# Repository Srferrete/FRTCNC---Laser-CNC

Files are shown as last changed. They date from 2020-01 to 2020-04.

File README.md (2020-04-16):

# Laser-CNC
Maquina Cnc para poder poner un laser y hacer grabados 

Estamos creando un Laser cnc, que pueda ser construido a mediante piezas impresas en 3d y material basico con el fin de que sea lo más sencilla de montar y lo más barata posible.

Es un proyecto que ya hicimos el pasado, pero esta vez le hemos dado una vuelta para que quede lo más vistoso posible además de hacer una estructura un poco más fuerte.

La base de la maquina es basante sencilla, vas a usar Perfiles V-slot, perfilería de aluminio y materiales basicos.
En cuanto a electronica usaremos un Mks DLC con driver Drv8825 y como FirmWare nos basaremos en GRBL.
MONTAJE
Todo el montaje y configuración lo podeis encontrar en mi canal de youtube, no os lo perdais y suscribiros.
https://www.youtube.com/playlist?list=PL0HtuDn0Yw6M-yycOaHozkW66rjWwoKbI

FIRMWARE
Para instalar el firmware en la MKS DLC, necesitais instalar el IDE de arduino que podeis encontrar aqui https://www.arduino.cc/
Una vez instalado, copiar la carpeta grbl en en C:\Users\VUESTRO_USUARIO\Documents\Arduino\libraries. De esta manera os funcionará como lo hacemos en el video.

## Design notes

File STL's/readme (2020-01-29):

Esta Carpeta Os dejo todos los stl relacionanos con la máquina laser aunque tambien los podeis encontrar en thingiverse(está pendiente de subir)
Tambien os iré dejando por aquí enlaces a piezas de thingiverse que usado para mi cnc, como por ejemplo
el soporete de los finales de carrera

PIEZAS DE OTROS DISEÑADORES

soporte finales de carrera -- https://www.thingiverse.com/thing:3147644

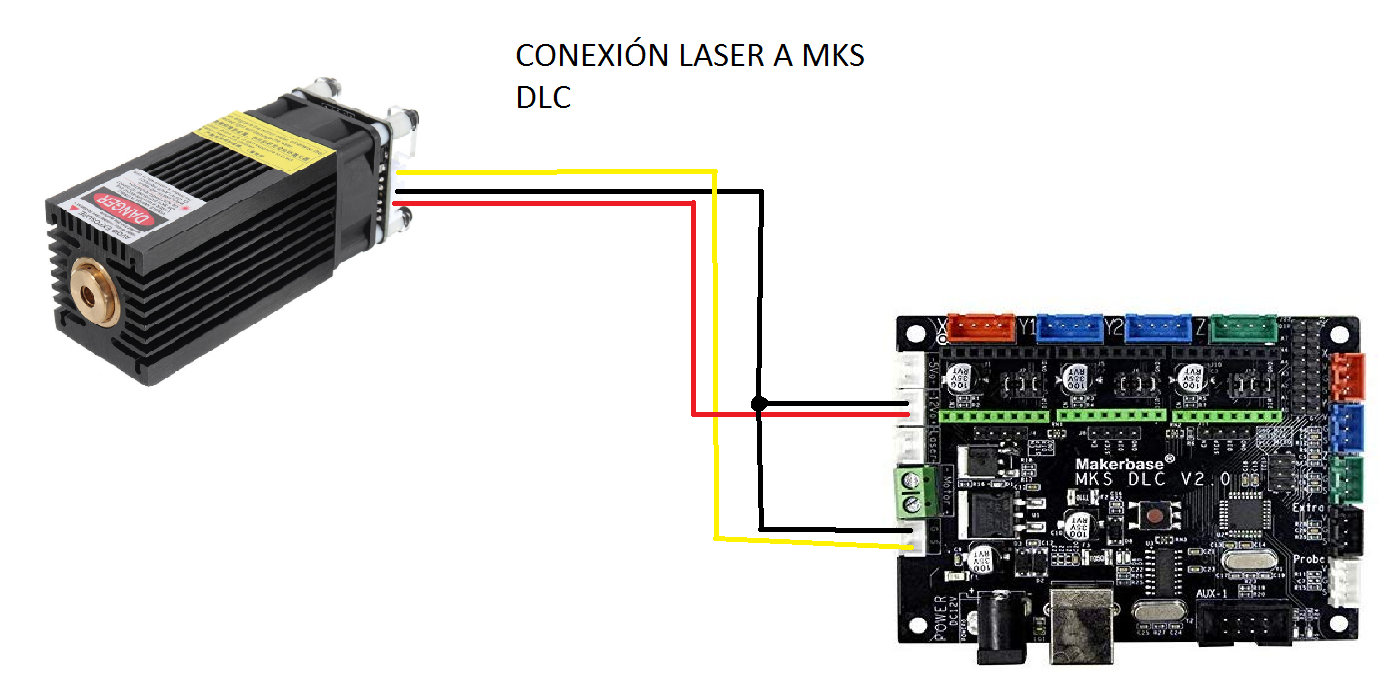
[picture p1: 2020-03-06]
Conexion laser a Mks DLC.png

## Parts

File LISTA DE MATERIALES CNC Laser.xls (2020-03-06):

MATERIAL | CANTIDAD | MEDIDA | ENLACES | ENLACES - OPCION 2 | NOTAS | precio
Perfil V-Slot 2040 | 3 | 500mm | http://store.thingibox.com/es/mecanica/187-extrusion_v-slot_20x40.html | https://www.banggood.com/custlink/GKvmsnZmI6
Perfil aluminio 20x20mm 1.5mm grosor | 2 | 451mm | https://bit.ly/2ReEGch
Varilla roscada M12 | 2 | 530mm | https://bit.ly/38b0EmK
Tuercas M12 | 4
Arandelas M12 | 4
Ruedas Vslot | 12 |  | https://amzn.to/38VEWTt | https://www.banggood.com/custlink/3mmKsnZKSf
Separadores Excentricos | 6 |  | https://amzn.to/2LjGrBn | https://www.banggood.com/custlink/KGvKAQivaL
Separadores de 6mm | 10 | 6mm | https://bit.ly/2rPHEcC |  | Pueden Ser metalicos o de nylon
Arandelas M5 - 1mm Grosor(precision) | 32 |  | https://bit.ly/2YbtXAV
Polea GT2 16 dientes | 3 |  | https://amzn.to/361GNob | https://www.banggood.com/custlink/3D33NbiDO1
Correa GT2 - 6mm | 3 | 600mm | https://amzn.to/2rNy1Ly | https://www.banggood.com/custlink/mvDGsbi3gR | Normalmente se venden 5 metros de sobra icluso para equivocarnos
Turecas tipo martillo M4 | 8 |  | https://amzn.to/33PS75m | https://www.banggood.com/custlink/GmKmssZv6s | Para sujeción de correas y finales de carrera
Tornillos M3x8 | 12 | 8mm |  |  | Para anclar los motores
Arandelas M3 | 12
Tuercas autoblocantes M5 | 12
Tornillos M5x25 | 8 | 25mm |  |  | Para atornillas las patas a los perfiles
Tornillos M5x14 | 4 | 14mm |  |  | Para atornillar los paneles laterales al perfil del Eje X
Tornillos M5x30 | 8 | 30mm |  |  | Para sujetar ruedas en los ejes Y
Tornillso M4x40 | 4 | 40mm |  |  | Para sujetar ruedas en el Eje X
Varilla roscada M5 | 1 | 135mm
Tornillos M4x10 | 8 | 10mm |  |  | Para sujeción de correas y finales de carrera
Tornillos M2x8 | 4 | 8mm |  |  | Para los finales de carrera
Motores Nema 17 - 1,5 Amp | 3 |  | https://amzn.to/2r7OiLe | https://www.banggood.com/custlink/KvDvAb9DsG | Realmente podemos usar cualquer nema 17
MKS DLC | 1 |  | https://es.aliexpress.com/item/1000007228357.html?spm=a2g0s.9042311.0.0.260b63c0Zrzpdr
Drivers DRV8825 | 2 |  | https://amzn.to/2rNxBEY | https://www.banggood.com/custlink/mGDGnAZ3Ac
kit terminales jst + dupont + cripadora | MUCHOS |  | https://amzn.to/397kIpN | https://www.banggood.com/custlink/vmK3sUe7pV | Aconsejo el amazon es más completo
Cables para motores | 3 | varias medidas | https://amzn.to/39f3AP1 | https://www.banggood.com/custlink/3mvDbqgTr2
Cadena de Arrastre |  | OPCIONAL | https://amzn.to/2w1uueA
finales de carrera | 2 |  | https://amzn.to/2vvWAP3
Transformador 12v 10 Amperios | 1 |  | https://amzn.to/37MMAyk | https://www.banggood.com/custlink/Kv3GqyDAwA | El de banggood es de 8 amperios pero tambien nos vale
Laser Al gusto |  |  |  |  | Os dejo enlaces de ejemplo compatibles con el enganche de la maquina.
 |  |  |  | LASER 7W PWM | https://www.banggood.com/custlink/mDGvQAZDkK
 |  |  |  | LASER 3,5W PWM - es el que tengo en casa | https://www.banggood.com/custlink/vm3GNnIKkJ

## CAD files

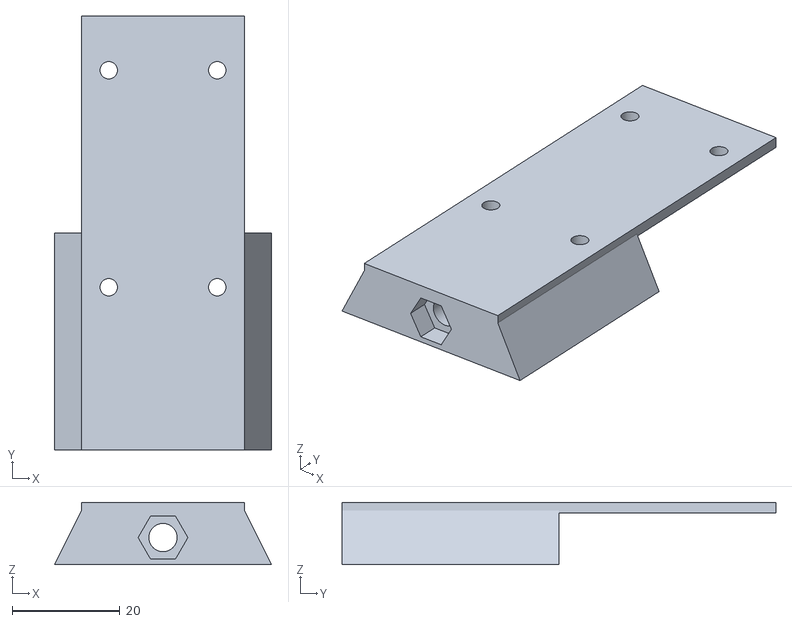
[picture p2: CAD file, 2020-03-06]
STL's/soporte laser V2.stl
40.2 x 80.4 x 11.6

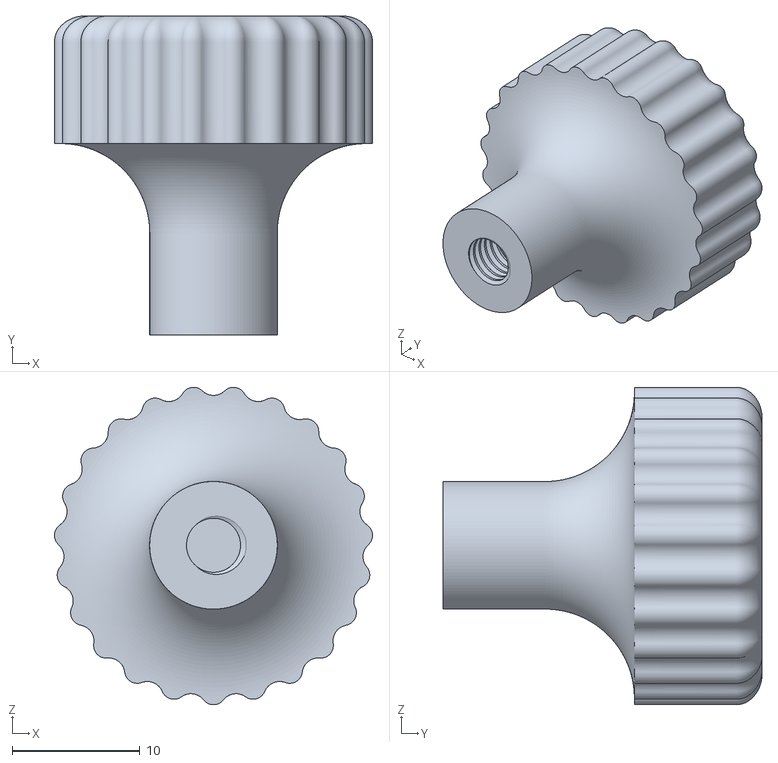
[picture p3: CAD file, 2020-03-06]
STL's/ruleta grande.stl
24.9 x 25.0 x 24.9

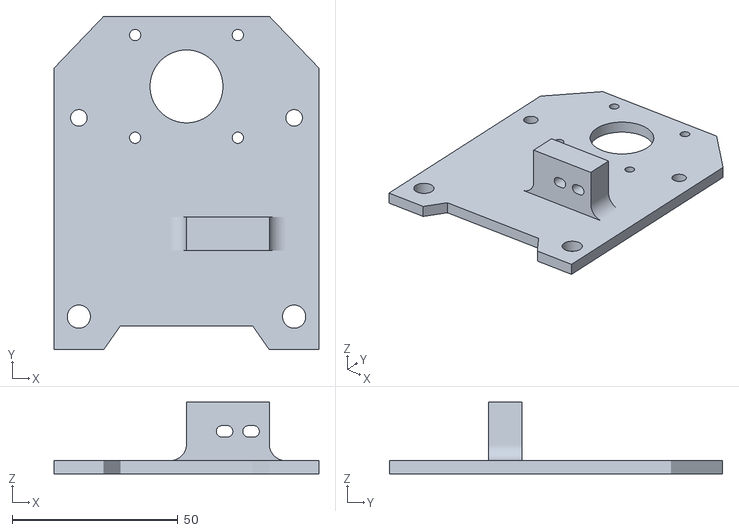
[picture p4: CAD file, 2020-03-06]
STL's/Posterior con cadeneta.stl
80.0 x 100.7 x 21.7

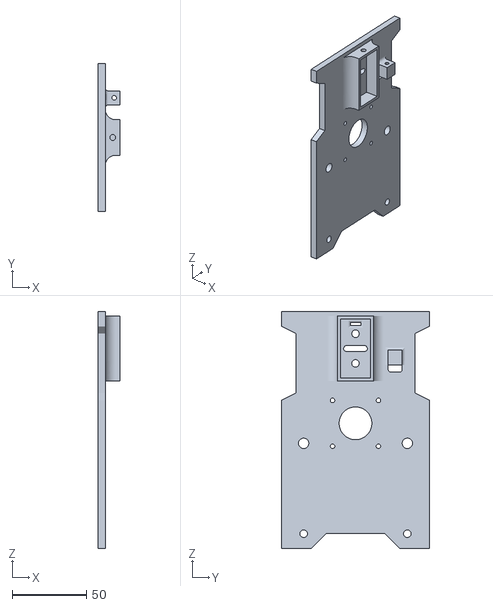
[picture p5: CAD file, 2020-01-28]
STL's/carro eje Y Izquierda.stl
15.0 x 100.0 x 160.0

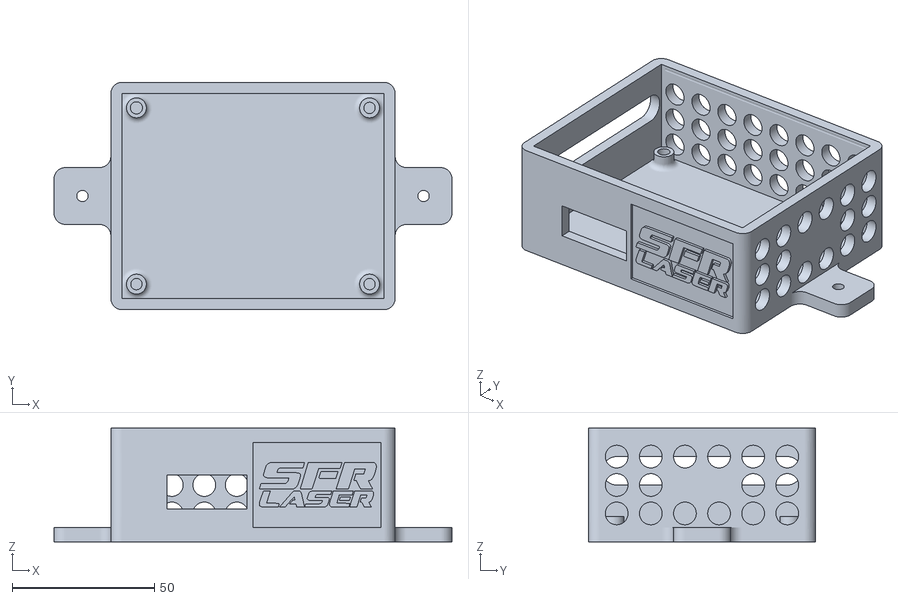
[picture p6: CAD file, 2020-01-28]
STL's/caja MKS_DLC.stl
140.0 x 80.0 x 40.0

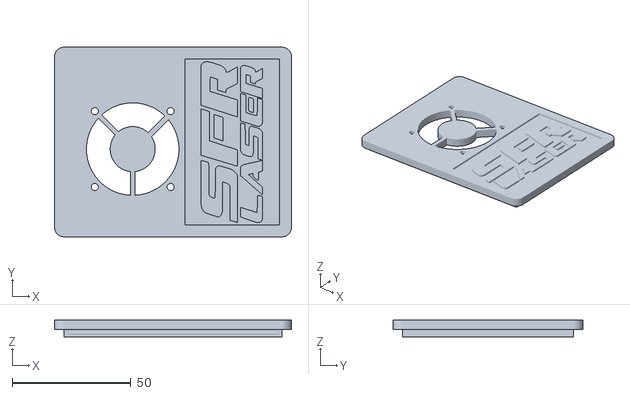
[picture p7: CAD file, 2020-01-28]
STL's/Tapa caja.stl
100.0 x 80.0 x 7.00

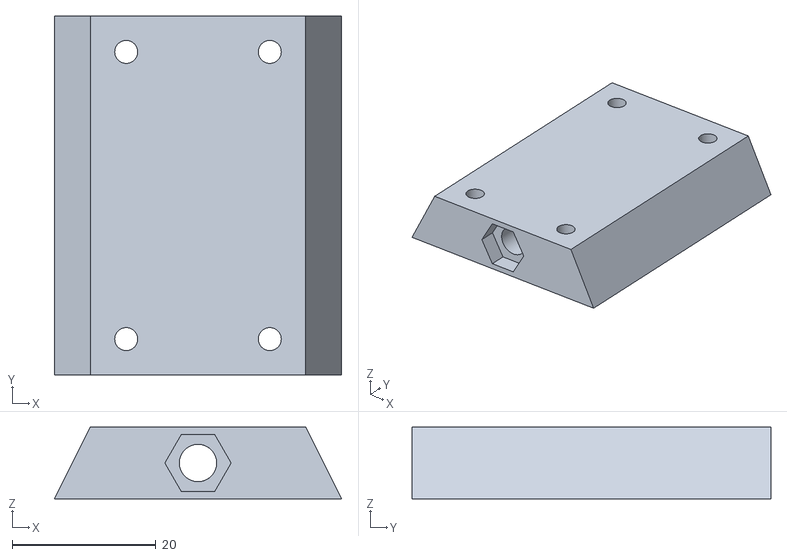
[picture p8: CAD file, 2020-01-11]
STL's/soporte_Laser.stl
40.0 x 50.0 x 10.00

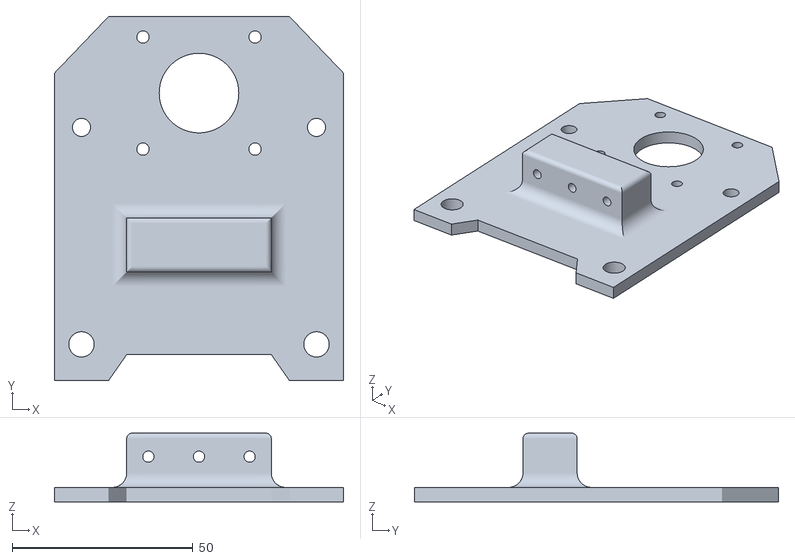
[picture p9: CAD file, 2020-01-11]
STL's/Carro_X_trasera.stl
80.0 x 100.7 x 19.0

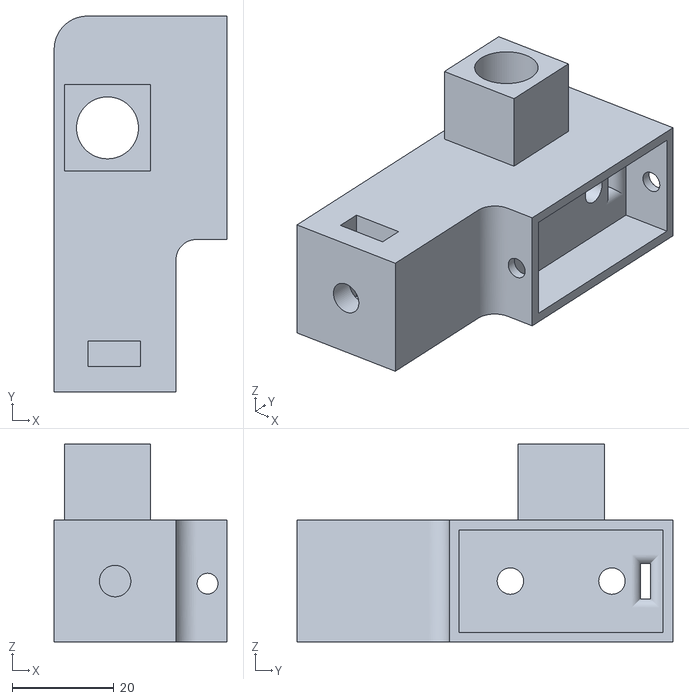
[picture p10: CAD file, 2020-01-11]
STL's/Junta_esquina Izquierda.stl
34.0 x 74.0 x 39.0

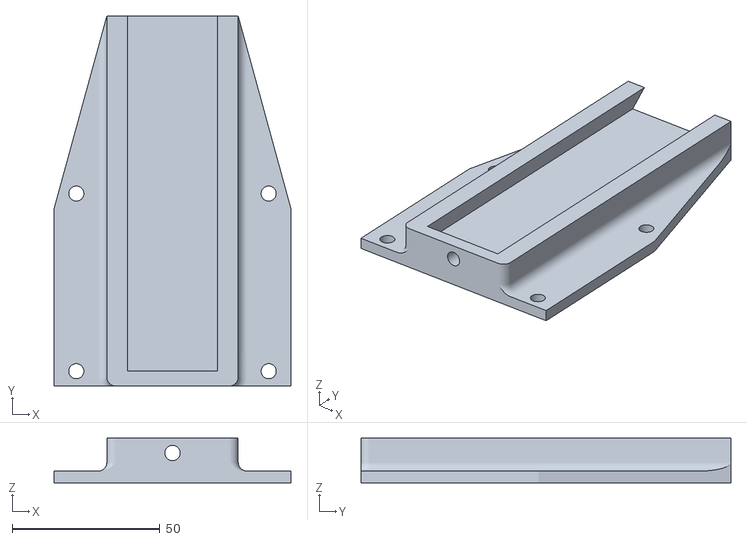
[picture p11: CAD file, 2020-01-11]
STL's/Carro_X_delantera.stl
80.0 x 125.0 x 15.2

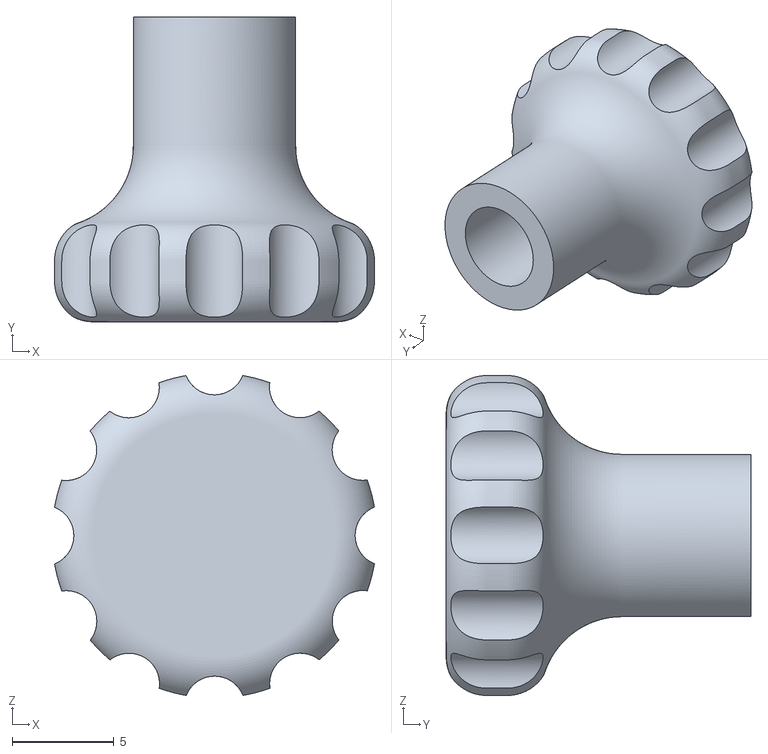
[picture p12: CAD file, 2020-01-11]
STL's/Rueda.stl
15.8 x 15.0 x 15.8

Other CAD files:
STL's/carro eje Y derecha.stl
STL's/Junta_esquina Derecha.stl
diseños fusion/CarroX_anterior_v3.1 v11.f3d
diseños fusion/CarroX_anterior_v3.1_Con_Cadeneta v4.f3d
diseños fusion/CarroX_v3.1 v5.f3d
diseños fusion/Carro_Y_V4 v6.f3d
diseños fusion/Junta_esquina_laser V4 - Contensor de correa v4.f3d
diseños fusion/caja MKS_DLC.f3d

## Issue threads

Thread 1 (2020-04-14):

GRBL

Nichelsar, 2020-04-14:
Estoy teniendo problemas para encontrar el GRBL que mencionas has colgado.
En cuanto a las especificaciones que realizas en tu video, el controlador que uso, no deja de mandarme error 20, puedo manejar perfectamente la cortadora laser, pero el homing no me lo hace de ninguna de las formas.
Si puedes cuelga tu configuración  y lo intento con esa, a ver si puedo ya que uso exactamente el mismo hardware que usas tu.
Gracias por tu trabajo

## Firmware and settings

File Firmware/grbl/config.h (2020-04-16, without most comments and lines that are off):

#define config_h
#include "grbl.h" // For Arduino IDE compatibility.
#define DEFAULTS_GENERIC
#define CPU_MAP_ATMEGA328P // Arduino Uno CPU
#define BAUD_RATE 115200
#define CMD_RESET 0x18 // ctrl-x.
#define CMD_STATUS_REPORT '?'
#define CMD_CYCLE_START '~'
#define CMD_FEED_HOLD '!'
#define CMD_CYCLE_START 0x82
#define CMD_SAFETY_DOOR 0x84
#define CMD_JOG_CANCEL  0x85
#define CMD_DEBUG_REPORT 0x86 // Only when DEBUG enabled, sends debug report in '{}' braces.
#define CMD_FEED_OVR_RESET 0x90         // Restores feed override value to 100%.
#define CMD_FEED_OVR_COARSE_PLUS 0x91
#define CMD_FEED_OVR_COARSE_MINUS 0x92
#define CMD_FEED_OVR_FINE_PLUS  0x93
#define CMD_FEED_OVR_FINE_MINUS  0x94
#define CMD_RAPID_OVR_RESET 0x95        // Restores rapid override value to 100%.
#define CMD_RAPID_OVR_MEDIUM 0x96
#define CMD_RAPID_OVR_LOW 0x97
#define CMD_SPINDLE_OVR_RESET 0x99      // Restores spindle override value to 100%.
#define CMD_SPINDLE_OVR_COARSE_PLUS 0x9A
#define CMD_SPINDLE_OVR_COARSE_MINUS 0x9B
#define CMD_SPINDLE_OVR_FINE_PLUS 0x9C
#define CMD_SPINDLE_OVR_FINE_MINUS 0x9D
#define CMD_SPINDLE_OVR_STOP 0x9E
#define CMD_COOLANT_FLOOD_OVR_TOGGLE 0xA0
#define CMD_COOLANT_MIST_OVR_TOGGLE 0xA1
#define HOMING_CYCLE_0 ((1<<X_AXIS)|(1<<Y_AXIS))  // NOT COMPATIBLE WITH COREXY: Homes both X-Y in one cycle.
#define N_HOMING_LOCATE_CYCLE 1 // Integer (1-128)
#define N_STARTUP_LINE 2 // Integer (1-2)
#define N_DECIMAL_COORDVALUE_INCH 4 // Coordinate or position value in inches
#define N_DECIMAL_COORDVALUE_MM   3 // Coordinate or position value in mm
#define N_DECIMAL_RATEVALUE_INCH  1 // Rate or velocity value in in/min
#define N_DECIMAL_RATEVALUE_MM    0 // Rate or velocity value in mm/min
#define N_DECIMAL_SETTINGVALUE    3 // Decimals for floating point setting values
#define N_DECIMAL_RPMVALUE        0 // RPM value in rotations per min.
#define MESSAGE_PROBE_COORDINATES // Enabled by default. Comment to disable.
#define SAFETY_DOOR_SPINDLE_DELAY 4.0 // Float (seconds)
#define SAFETY_DOOR_COOLANT_DELAY 1.0 // Float (seconds)
#define CHECK_LIMITS_AT_INIT
#define DEFAULT_FEED_OVERRIDE           100 // 100%. Don't change this value.
#define MAX_FEED_RATE_OVERRIDE          200 // Percent of programmed feed rate (100-255). Usually 120% or 200%
#define MIN_FEED_RATE_OVERRIDE           10 // Percent of programmed feed rate (1-100). Usually 50% or 1%
#define FEED_OVERRIDE_COARSE_INCREMENT   10 // (1-99). Usually 10%.
#define FEED_OVERRIDE_FINE_INCREMENT      1 // (1-99). Usually 1%.
#define DEFAULT_RAPID_OVERRIDE  100 // 100%. Don't change this value.
#define RAPID_OVERRIDE_MEDIUM    50 // Percent of rapid (1-99). Usually 50%.
#define RAPID_OVERRIDE_LOW       25 // Percent of rapid (1-99). Usually 25%.
#define DEFAULT_SPINDLE_SPEED_OVERRIDE    100 // 100%. Don't change this value.
#define MAX_SPINDLE_SPEED_OVERRIDE        200 // Percent of programmed spindle speed (100-255). Usually 200%.
#define MIN_SPINDLE_SPEED_OVERRIDE         10 // Percent of programmed spindle speed (1-100). Usually 10%.
#define SPINDLE_OVERRIDE_COARSE_INCREMENT  10 // (1-99). Usually 10%.
#define SPINDLE_OVERRIDE_FINE_INCREMENT     1 // (1-99). Usually 1%.
#define RESTORE_OVERRIDES_AFTER_PROGRAM_END // Default enabled. Comment to disable.
#define REPORT_FIELD_BUFFER_STATE // Default enabled. Comment to disable.
#define REPORT_FIELD_PIN_STATE // Default enabled. Comment to disable.
#define REPORT_FIELD_CURRENT_FEED_SPEED // Default enabled. Comment to disable.
#define REPORT_FIELD_WORK_COORD_OFFSET // Default enabled. Comment to disable.
#define REPORT_FIELD_OVERRIDES // Default enabled. Comment to disable.
#define REPORT_FIELD_LINE_NUMBERS // Default enabled. Comment to disable.
#define REPORT_OVR_REFRESH_BUSY_COUNT 20  // (1-255)
#define REPORT_OVR_REFRESH_IDLE_COUNT 10  // (1-255) Must be less than or equal to the busy count
#define REPORT_WCO_REFRESH_BUSY_COUNT 30  // (2-255)
#define REPORT_WCO_REFRESH_IDLE_COUNT 10  // (2-255) Must be less than or equal to the busy count
#define ACCELERATION_TICKS_PER_SECOND 100
#define ADAPTIVE_MULTI_AXIS_STEP_SMOOTHING  // Default enabled. Comment to disable.
#define TOOL_LENGTH_OFFSET_AXIS Z_AXIS // Default z-axis. Valid values are X_AXIS, Y_AXIS, or Z_AXIS.
#define VARIABLE_SPINDLE // Default enabled. Comment to disable.
#define MINIMUM_JUNCTION_SPEED 0.0 // (mm/min)
#define MINIMUM_FEED_RATE 1.0 // (mm/min)
#define N_ARC_CORRECTION 12 // Integer (1-255)
#define ARC_ANGULAR_TRAVEL_EPSILON 5E-7 // Float (radians)
#define DWELL_TIME_STEP 50 // Integer (1-255) (milliseconds)
#define ENABLE_RESTORE_EEPROM_WIPE_ALL         // '$RST=*' Default enabled. Comment to disable.
#define ENABLE_RESTORE_EEPROM_DEFAULT_SETTINGS // '$RST=$' Default enabled. Comment to disable.
#define ENABLE_RESTORE_EEPROM_CLEAR_PARAMETERS // '$RST=#' Default enabled. Comment to disable.
#define ENABLE_BUILD_INFO_WRITE_COMMAND // '$I=' Default enabled. Comment to disable.
#define FORCE_BUFFER_SYNC_DURING_EEPROM_WRITE // Default enabled. Comment to disable.
#define FORCE_BUFFER_SYNC_DURING_WCO_CHANGE // Default enabled. Comment to disable.
#define PARKING_AXIS Z_AXIS // Define which axis that performs the parking motion
#define PARKING_TARGET -5.0 // Parking axis target. In mm, as machine coordinate [-max_travel,0].
#define PARKING_RATE 500.0 // Parking fast rate after pull-out in mm/min.
#define PARKING_PULLOUT_RATE 100.0 // Pull-out/plunge slow feed rate in mm/min.
#define PARKING_PULLOUT_INCREMENT 5.0 // Spindle pull-out and plunge distance in mm. Incremental distance.
#define DISABLE_LASER_DURING_HOLD // Default enabled. Comment to disable.
#define N_PIECES 4  // Integer (1-4). Number of piecewise lines used in script solution.
#define RPM_MAX  11686.4  // Max RPM of model. $30 > RPM_MAX will be limited to RPM_MAX.
#define RPM_MIN  202.5    // Min RPM of model. $31 < RPM_MIN will be limited to RPM_MIN.
#define RPM_POINT12  6145.4  // Used N_PIECES >=2. Junction point between lines 1 and 2.
#define RPM_POINT23  9627.8  // Used N_PIECES >=3. Junction point between lines 2 and 3.
#define RPM_POINT34  10813.9 // Used N_PIECES = 4. Junction point between lines 3 and 4.
#define RPM_LINE_A1  3.197101e-03  // Used N_PIECES >=1. A and B constants of line 1.
#define RPM_LINE_B1  -3.526076e-1
#define RPM_LINE_A2  1.722950e-2   // Used N_PIECES >=2. A and B constants of line 2.
#define RPM_LINE_B2  8.588176e+01
#define RPM_LINE_A3  5.901518e-02  // Used N_PIECES >=3. A and B constants of line 3.
#define RPM_LINE_B3  4.881851e+02
#define RPM_LINE_A4  1.203413e-01  // Used N_PIECES = 4. A and B constants of line 4.
#define RPM_LINE_B4  1.151360e+03
#define DUAL_AXIS_SELECT  X_AXIS  // Must be either X_AXIS or Y_AXIS
#define DUAL_AXIS_HOMING_FAIL_AXIS_LENGTH_PERCENT  5.0  // Float (percent)
#define DUAL_AXIS_HOMING_FAIL_DISTANCE_MAX  25.0  // Float (mm)
#define DUAL_AXIS_HOMING_FAIL_DISTANCE_MIN  2.5  // Float (mm)
#define DUAL_AXIS_CONFIG_PROTONEER_V3_51    // Uncomment to select. Comment other configs.

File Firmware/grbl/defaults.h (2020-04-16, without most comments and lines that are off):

  #define DEFAULT_X_STEPS_PER_MM 80.0
  #define DEFAULT_Y_STEPS_PER_MM 80.0
  #define DEFAULT_Z_STEPS_PER_MM 800.0 //no Usado
  #define DEFAULT_X_MAX_RATE 6000.0 // mm/min
  #define DEFAULT_Y_MAX_RATE 6000.0 // mm/min
  #define DEFAULT_Z_MAX_RATE 5000.0 // mm/min
  #define DEFAULT_X_ACCELERATION (10.0*60*60) // 10*60*60 mm/min^2 = 10 mm/sec^2
  #define DEFAULT_Y_ACCELERATION (10.0*60*60) // 10*60*60 mm/min^2 = 10 mm/sec^2
  #define DEFAULT_Z_ACCELERATION (10.0*60*60) // 10*60*60 mm/min^2 = 10 mm/sec^2
  #define DEFAULT_X_MAX_TRAVEL 400.0 // mm NOTE: Must be a positive value.
  #define DEFAULT_Y_MAX_TRAVEL 400.0 // mm NOTE: Must be a positive value.
  #define DEFAULT_Z_MAX_TRAVEL 200.0 // mm NOTE: Must be a positive value. No usado
  #define DEFAULT_SPINDLE_RPM_MAX 1000.0 // rpm
  #define DEFAULT_SPINDLE_RPM_MIN 0.0 // rpm
  #define DEFAULT_STEP_PULSE_MICROSECONDS 20
  #define DEFAULT_STEPPING_INVERT_MASK 0
  #define DEFAULT_DIRECTION_INVERT_MASK 0
  #define DEFAULT_STEPPER_IDLE_LOCK_TIME 25 // msec (0-254, 255 keeps steppers enabled)
  #define DEFAULT_STATUS_REPORT_MASK 1 // MPos enabled
  #define DEFAULT_JUNCTION_DEVIATION 0.01 // mm
  #define DEFAULT_ARC_TOLERANCE 0.002 // mm
  #define DEFAULT_REPORT_INCHES 0 // false
  #define DEFAULT_INVERT_ST_ENABLE 0 // false
  #define DEFAULT_INVERT_LIMIT_PINS 0 // false
  #define DEFAULT_SOFT_LIMIT_ENABLE 1 // false
  #define DEFAULT_HARD_LIMIT_ENABLE 1  // false
  #define DEFAULT_INVERT_PROBE_PIN 0 // false
  #define DEFAULT_LASER_MODE 1 // false
  #define DEFAULT_HOMING_ENABLE 1  // false
  #define DEFAULT_HOMING_DIR_MASK 0 // move positive dir
  #define DEFAULT_HOMING_FEED_RATE 600.0 // mm/min
  #define DEFAULT_HOMING_SEEK_RATE 1000.0 // mm/min
  #define DEFAULT_HOMING_DEBOUNCE_DELAY 250 // msec (0-65k)
  #define DEFAULT_HOMING_PULLOFF 2.0 // mm
#ifdef DEFAULTS_SHERLINE_5400
  #define MICROSTEPS 2
  #define STEPS_PER_REV 200.0
  #define MM_PER_REV (0.050*MM_PER_INCH) // 0.050 inch/rev leadscrew
  #define DEFAULT_X_STEPS_PER_MM (STEPS_PER_REV*MICROSTEPS/MM_PER_REV)
  #define DEFAULT_Y_STEPS_PER_MM (STEPS_PER_REV*MICROSTEPS/MM_PER_REV)
  #define DEFAULT_Z_STEPS_PER_MM (STEPS_PER_REV*MICROSTEPS/MM_PER_REV)
  #define DEFAULT_X_MAX_RATE 635.0 // mm/min (25 ipm)
  #define DEFAULT_Y_MAX_RATE 635.0 // mm/min
  #define DEFAULT_Z_MAX_RATE 635.0 // mm/min
  #define DEFAULT_X_ACCELERATION (50.0*60*60) // 50*60*60 mm/min^2 = 50 mm/sec^2
  #define DEFAULT_Y_ACCELERATION (50.0*60*60) // 50*60*60 mm/min^2 = 50 mm/sec^2
  #define DEFAULT_Z_ACCELERATION (50.0*60*60) // 50*60*60 mm/min^2 = 50 mm/sec^2
  #define DEFAULT_X_MAX_TRAVEL 225.0 // mm NOTE: Must be a positive value.
  #define DEFAULT_Y_MAX_TRAVEL 125.0 // mm NOTE: Must be a positive value.
  #define DEFAULT_Z_MAX_TRAVEL 170.0 // mm NOTE: Must be a positive value.
  #define DEFAULT_SPINDLE_RPM_MAX 2800.0 // rpm
  #define DEFAULT_SPINDLE_RPM_MIN 0.0 // rpm
  #define DEFAULT_STEP_PULSE_MICROSECONDS 10
  #define DEFAULT_STEPPING_INVERT_MASK 0
  #define DEFAULT_DIRECTION_INVERT_MASK ((1<<Y_AXIS)|(1<<Z_AXIS))
  #define DEFAULT_STEPPER_IDLE_LOCK_TIME 25 // msec (0-254, 255 keeps steppers enabled)
  #define DEFAULT_STATUS_REPORT_MASK 1 // MPos enabled
  #define DEFAULT_JUNCTION_DEVIATION 0.01 // mm
  #define DEFAULT_ARC_TOLERANCE 0.002 // mm
  #define DEFAULT_REPORT_INCHES 0 // true
  #define DEFAULT_INVERT_ST_ENABLE 0 // false
  #define DEFAULT_INVERT_LIMIT_PINS 0 // false
  #define DEFAULT_SOFT_LIMIT_ENABLE 0 // false
  #define DEFAULT_HARD_LIMIT_ENABLE 0  // false
  #define DEFAULT_INVERT_PROBE_PIN 0 // false
  #define DEFAULT_LASER_MODE 0 // false
  #define DEFAULT_HOMING_ENABLE 0  // false
  #define DEFAULT_HOMING_DIR_MASK 0 // move positive dir
  #define DEFAULT_HOMING_FEED_RATE 50.0 // mm/min
  #define DEFAULT_HOMING_SEEK_RATE 635.0 // mm/min
  #define DEFAULT_HOMING_DEBOUNCE_DELAY 250 // msec (0-65k)
  #define DEFAULT_HOMING_PULLOFF 1.0 // mm
#endif
#ifdef DEFAULTS_POCKETNC_FR4
  #define DEFAULT_X_STEPS_PER_MM 800.0
  #define DEFAULT_Y_STEPS_PER_MM 800.0
  #define DEFAULT_Z_STEPS_PER_MM 800.0
  #define DEFAULT_X_MAX_RATE 300.0 // mm/min
  #define DEFAULT_Y_MAX_RATE 300.0 // mm/min
  #define DEFAULT_Z_MAX_RATE 300.0 // mm/min
  #define DEFAULT_X_ACCELERATION (30.0*60*60) // 15*60*60 mm/min^2 = 15 mm/sec^2
  #define DEFAULT_Y_ACCELERATION (30.0*60*60) // 15*60*60 mm/min^2 = 15 mm/sec^2
  #define DEFAULT_Z_ACCELERATION (30.0*60*60) // 15*60*60 mm/min^2 = 15 mm/sec^2
  #define DEFAULT_X_MAX_TRAVEL 225.0 // mm NOTE: Must be a positive value.
  #define DEFAULT_Y_MAX_TRAVEL 125.0 // mm NOTE: Must be a positive value.
  #define DEFAULT_Z_MAX_TRAVEL 170.0 // mm NOTE: Must be a positive value.
  #define DEFAULT_SPINDLE_RPM_MAX 7000.0 // rpm
  #define DEFAULT_SPINDLE_RPM_MIN 0.0 // rpm
  #define DEFAULT_STEP_PULSE_MICROSECONDS 10
  #define DEFAULT_STEPPING_INVERT_MASK 0
  #define DEFAULT_DIRECTION_INVERT_MASK ((1<<Y_AXIS)|(1<<Z_AXIS))
  #define DEFAULT_STEPPER_IDLE_LOCK_TIME 250 // msec (0-254, 255 keeps steppers enabled)
  #define DEFAULT_STATUS_REPORT_MASK 3 // WPos enabled
  #define DEFAULT_JUNCTION_DEVIATION 0.01 // mm
  #define DEFAULT_ARC_TOLERANCE 0.002 // mm
  #define DEFAULT_REPORT_INCHES 0 // false
  #define DEFAULT_INVERT_ST_ENABLE 1 // false
  #define DEFAULT_INVERT_LIMIT_PINS 0 // false
  #define DEFAULT_SOFT_LIMIT_ENABLE 0 // false
  #define DEFAULT_HARD_LIMIT_ENABLE 0  // false
  #define DEFAULT_INVERT_PROBE_PIN 0 // false
  #define DEFAULT_LASER_MODE 0 // false
  #define DEFAULT_HOMING_ENABLE 1  // false
  #define DEFAULT_HOMING_DIR_MASK 1 // move positive dir
  #define DEFAULT_HOMING_FEED_RATE 100.0 // mm/min
  #define DEFAULT_HOMING_SEEK_RATE 300.0 // mm/min
  #define DEFAULT_HOMING_DEBOUNCE_DELAY 250 // msec (0-65k)
  #define DEFAULT_HOMING_PULLOFF 3.0 // mm
#endif
#ifdef DEFAULTS_SHAPEOKO
  #define MICROSTEPS_XY 8
  #define STEP_REVS_XY 400
  #define MM_PER_REV_XY (0.08*18*MM_PER_INCH) // 0.08 in belt pitch, 18 pulley teeth
  #define MICROSTEPS_Z 2
  #define STEP_REVS_Z 400
  #define MM_PER_REV_Z 1.250 // 1.25 mm/rev leadscrew
  #define DEFAULT_X_STEPS_PER_MM (MICROSTEPS_XY*STEP_REVS_XY/MM_PER_REV_XY)
  #define DEFAULT_Y_STEPS_PER_MM (MICROSTEPS_XY*STEP_REVS_XY/MM_PER_REV_XY)
  #define DEFAULT_Z_STEPS_PER_MM (MICROSTEPS_Z*STEP_REVS_Z/MM_PER_REV_Z)
  #define DEFAULT_X_MAX_RATE 1000.0 // mm/min
  #define DEFAULT_Y_MAX_RATE 1000.0 // mm/min
  #define DEFAULT_Z_MAX_RATE 1000.0 // mm/min
  #define DEFAULT_X_ACCELERATION (15.0*60*60) // 15*60*60 mm/min^2 = 15 mm/sec^2
  #define DEFAULT_Y_ACCELERATION (15.0*60*60) // 15*60*60 mm/min^2 = 15 mm/sec^2
  #define DEFAULT_Z_ACCELERATION (15.0*60*60) // 15*60*60 mm/min^2 = 15 mm/sec^2
  #define DEFAULT_X_MAX_TRAVEL 200.0 // mm NOTE: Must be a positive value.
  #define DEFAULT_Y_MAX_TRAVEL 200.0 // mm NOTE: Must be a positive value.
  #define DEFAULT_Z_MAX_TRAVEL 200.0 // mm NOTE: Must be a positive value.
  #define DEFAULT_SPINDLE_RPM_MAX 10000.0 // rpm
  #define DEFAULT_SPINDLE_RPM_MIN 0.0 // rpm
  #define DEFAULT_STEP_PULSE_MICROSECONDS 10
  #define DEFAULT_STEPPING_INVERT_MASK 0
  #define DEFAULT_DIRECTION_INVERT_MASK ((1<<Y_AXIS)|(1<<Z_AXIS))
  #define DEFAULT_STEPPER_IDLE_LOCK_TIME 255 // msec (0-254, 255 keeps steppers enabled)
  #define DEFAULT_STATUS_REPORT_MASK 1 // MPos enabled
  #define DEFAULT_JUNCTION_DEVIATION 0.02 // mm
  #define DEFAULT_ARC_TOLERANCE 0.002 // mm
  #define DEFAULT_REPORT_INCHES 0 // false
  #define DEFAULT_INVERT_ST_ENABLE 0 // false
  #define DEFAULT_INVERT_LIMIT_PINS 0 // false
  #define DEFAULT_SOFT_LIMIT_ENABLE 0 // false
  #define DEFAULT_HARD_LIMIT_ENABLE 0  // false
  #define DEFAULT_INVERT_PROBE_PIN 0 // false
  #define DEFAULT_LASER_MODE 0 // false
  #define DEFAULT_HOMING_ENABLE 0  // false
  #define DEFAULT_HOMING_DIR_MASK 0 // move positive dir
  #define DEFAULT_HOMING_FEED_RATE 25.0 // mm/min
  #define DEFAULT_HOMING_SEEK_RATE 250.0 // mm/min
  #define DEFAULT_HOMING_DEBOUNCE_DELAY 250 // msec (0-65k)
  #define DEFAULT_HOMING_PULLOFF 1.0 // mm
#endif
#ifdef DEFAULTS_SHAPEOKO_2
  #define MICROSTEPS_XY 8
  #define STEP_REVS_XY 200
  #define MM_PER_REV_XY (2.0*20) // 2mm belt pitch, 20 pulley teeth
  #define MICROSTEPS_Z 2
  #define STEP_REVS_Z 200
  #define MM_PER_REV_Z 1.250 // 1.25 mm/rev leadscrew
  #define DEFAULT_X_STEPS_PER_MM (MICROSTEPS_XY*STEP_REVS_XY/MM_PER_REV_XY)
  #define DEFAULT_Y_STEPS_PER_MM (MICROSTEPS_XY*STEP_REVS_XY/MM_PER_REV_XY)
  #define DEFAULT_Z_STEPS_PER_MM (MICROSTEPS_Z*STEP_REVS_Z/MM_PER_REV_Z)
  #define DEFAULT_X_MAX_RATE 5000.0 // mm/min
  #define DEFAULT_Y_MAX_RATE 5000.0 // mm/min
  #define DEFAULT_Z_MAX_RATE 500.0 // mm/min
  #define DEFAULT_X_ACCELERATION (250.0*60*60) // 25*60*60 mm/min^2 = 25 mm/sec^2
  #define DEFAULT_Y_ACCELERATION (250.0*60*60) // 25*60*60 mm/min^2 = 25 mm/sec^2
  #define DEFAULT_Z_ACCELERATION (50.0*60*60) // 25*60*60 mm/min^2 = 25 mm/sec^2
  #define DEFAULT_X_MAX_TRAVEL 290.0 // mm NOTE: Must be a positive value.
  #define DEFAULT_Y_MAX_TRAVEL 290.0 // mm NOTE: Must be a positive value.
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

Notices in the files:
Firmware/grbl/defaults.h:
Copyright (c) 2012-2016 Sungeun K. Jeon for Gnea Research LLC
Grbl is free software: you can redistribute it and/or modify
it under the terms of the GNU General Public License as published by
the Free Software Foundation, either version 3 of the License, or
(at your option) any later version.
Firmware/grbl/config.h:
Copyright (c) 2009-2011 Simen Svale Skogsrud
